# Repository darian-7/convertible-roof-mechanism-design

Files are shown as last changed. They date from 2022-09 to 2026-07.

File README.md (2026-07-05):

# Convertible roof mechanism design (Fiat 595 Abarth)

**A full mechatronic design of a powered convertible roof for the Fiat 595 Abarth, from the MATLAB motor and damping dynamics to a Fusion 360 assembly and Arduino safety sensors.**





University of Bristol Year 2 Engineering Practice group project. The brief was to design a working powered roof for the Fiat 595 Abarth and carry it the whole way: market research and concept selection in Linkage, the mechanism dynamics in MATLAB, CAD and FEA in Fusion 360, material selection in Edupack, and a set of Arduino safety sensors, finishing with a bill of materials and a design review.

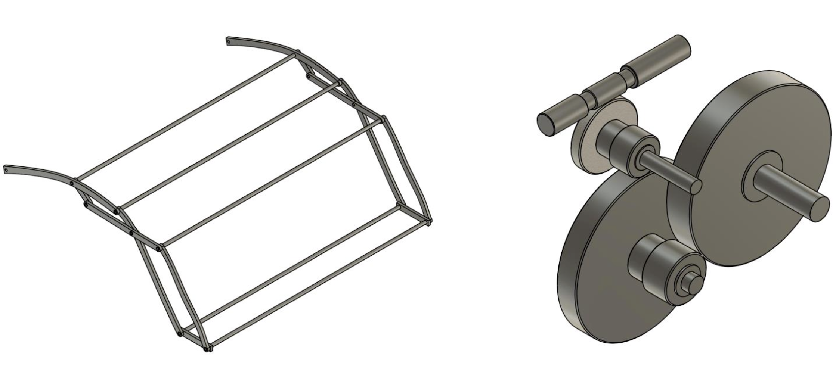
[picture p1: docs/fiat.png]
Fiat 595 Abarth


## What's inside

### Roof dynamics (`basic_model.m` and variants)
The roof is modelled as a driven rotating mechanism turned by a brushed DC motor. An ODE45 solver integrates the roof angle and angular velocity across the deploy and retract cycles from a torque balance: the motor's torque-speed line, gravity, viscous damping, aerodynamic drag read from a lookup table (`aero.m`), and a centre-of-mass radius that changes through the motion, exported from the Linkage model (`radius.m`). From that it computes torque, power, and energy for each candidate gear ratio. The deploy cycle came out at roughly 647 J. `GRAPHSFORREPORT.m` collects the design iterations (constant radius, variable radius, and the aero-plus-damping variants) into the report figures.

### Safety electronics (`docs/mechatronics_code.ino`)
Four sensors guard the mechanism so it cannot close on something or run at speed. An ultrasonic sensor watches for an obstruction above the roof, a capacitive sensor detects an object in the path, an anemometer reads wind speed, and a Hall-effect sensor counts wheel rotations to infer vehicle speed. If any of them crosses its threshold the motor stops. Two PWM channels drive the deploy and retract directions.

### CAD, kinematics, and materials
The Fusion 360 roof and gearbox assembly with FEA, the Linkage models used for concept kinematics and concept selection, and the Edupack material-selection study behind the chosen metal.

## Tech stack

MATLAB (mechanism dynamics, power and energy) · Autodesk Fusion 360 (CAD, FEA) · Linkage (2D mechanism kinematics) · Arduino (safety sensor firmware) · Granta Edupack (material selection)

## Repository structure

```
convertible-roof-mechanism-design/
├── docs/
│   ├── fiat.png                     # Fiat 595 Abarth reference
│   ├── mechatronics_code.ino        # Arduino safety-sensor firmware
│   ├── Group 1a *.pdf               # design / technical / manufacturing / mechatronics reports
│   ├── 545 Graphs/                  # deploy + retract torque, power, energy plots
│   ├── Linkage/                     # concept kinematics + concept selection
│   └── Material Selection/          # Edupack indices + weighted matrix
└── src/
    ├── basic_model*.m               # roof dynamics (motor, gravity, damping, aero)
    ├── aero.m, damping.m, radius.m  # torque contributions + variable COM radius
    ├── GRAPHSFORREPORT.m            # report figures across design iterations
    └── *.f3d                        # Fusion 360 roof + gearbox CAD
```

## Notes

Group coursework project, shared as a portfolio reference. Please don't submit any of it as your own.

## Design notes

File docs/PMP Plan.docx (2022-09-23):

# Template Project Management Plan

# 1 Introduction

The aim of this project is to produce a detailed design report for a convertible Fiat 595 Abarth that puts itself in direct competition with the BMW Mini Cooper convertible. Acting as the engineering team at Abarth, the following report presents a ‘proof-of-concept design’ for the Fiat with the goal of taking the idea forward into detailing and production based on the concept’s viability for a convertible 595 Abarth.

# 2 Project scope

Scope of project (Work Breakdown Structure):

- Market research, stakeholders, and priorities with a PDS.
- Concept selection using FBDs, Lego, and Linkage + CAD design.
- Modelling: motor and gear ratio combinations, system damping, gearbox efficiency, COM, mechanical power, power vs torque graph, radius vs angle of mechanism graph, angle vs time for retracting/deploying mechanism graph, mechanical power vs time.
- Manufacturing planning of chosen component + technical CAD drawing.
- Material selection and costing of all materials intended to use.
- Mechatronics report on chosen safety features and their respective sensors for the convertible roof mechanism.
- Motor and gear combination choices + CAD design of gearbox.
- Design evaluation of success of entire proposed report highlighting successes and failures.

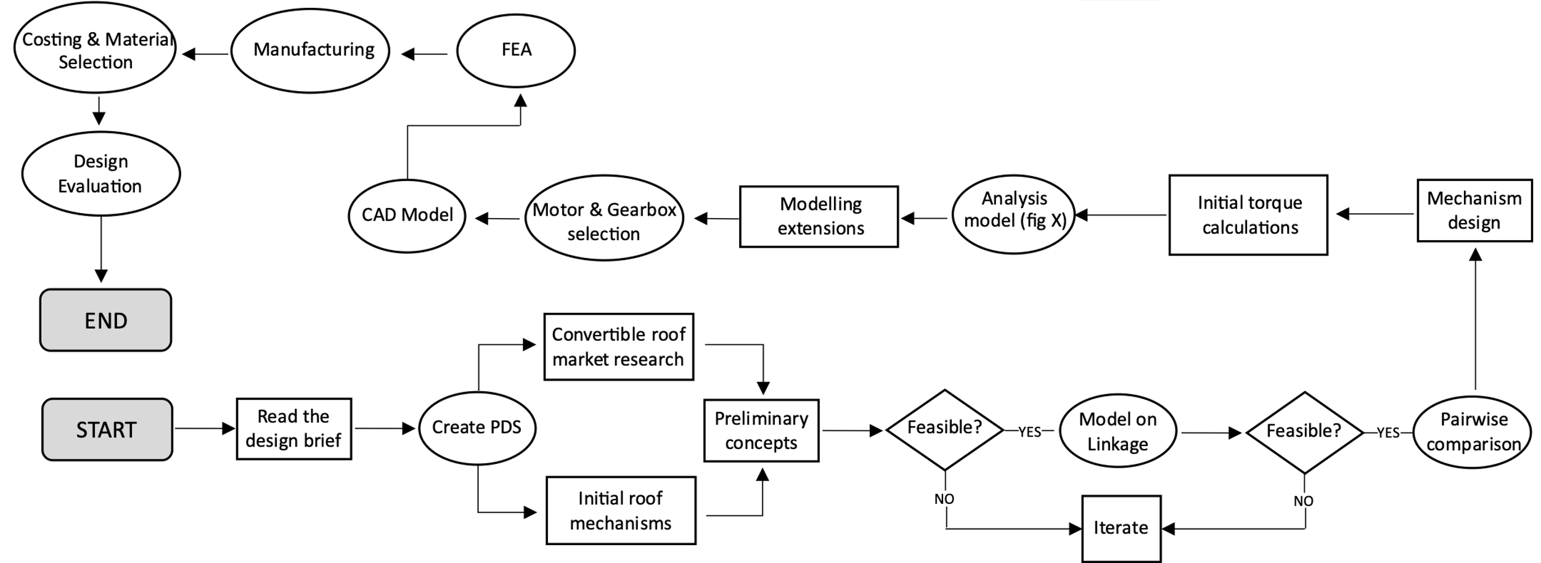
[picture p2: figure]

Not in the scope of project:

- Real-life sensor functionality with car based on its intended use.
- Real-life testing of retracting/deploying roof mechanism of Fiat 595 Abarth.
- Real-life testing of the chosen gear ratios and selected motor.
- Testing the life-cycle of the convertible Fiat 595 Abarth as it is not manufactured yet.
- Market research involving surveys to identify the needs of the required target market, not in the scope of the project due to time constraints.

## Key success criteria

- Come up with safety features that put the safety of the passengers and convertible roof mechanism as utmost priority.
- Design convertible roof report that contains similar features to the convertible Mini Cooper and remains within a similar price bracket to put it in direct competition with the convertible Mini.
- Conduct sufficient market research
- Aim to meet most, if not all of the requirements listed in the PDS of the report.
- Aim to stay in track with the recommended timelines given to us in the brief.
- Run iterations and constantly develop concepts and design decisions to produce the best possible ‘proof of design’ report. Important to do this throughout the report and not at the end of the report.

## 2.1 Project assumptions

- Assumption 1: Group 1 acts as the engineering team at Abarth and the project is a ‘proof of design’ report made with the goal of taking the convertible roof idea forward into detailing and production for the Fiat 595 Abarth to put it in direct competition with the convertible Mini Cooper.
- Assumption 2: Us as the engineering team has access all components required to manufacture the convertible roof: Roof bracket, motor, chosen gears, chosen sensors, manufacturing methods.
- Assumption 3: Us as the engineering team have the budget to manufacture the components of the roof and conduct any required R&D throughout the design of the convertible roof mechanism.

# 3 Project team & stakeholders

Role | Responsibility | Who
Market research and PDS requirements | Market research on convertible roof concepts and features of BMW Mini Cooper convertible. Constructing a PDS which provides guidance for chosen design decisions and concepts. | Darian
Manufacturing, material selection and costing | Details on manufacturing process of chosen component. Material selection process with appropriate justifications. Costing of chosen components need to manufacture the convertible roof mechanism. | Andhika, Darian
Drawings | Complete technical drawing of chosen component. Complete assembly drawing of the roof. Layout diagram showing gearbox arrangement. All drawings done on Fusion 360. | Andhika
Motor, gears, and gearbox | Selection of motor and gear ratio. Gearbox arrangement based on required system energy and torque. | Viral and Andhika
Modelling | Model of inverse pendulum, motor/gear combinations, gearbox efficiency, system energy use and COM. All calculations are coded on MATLAB and the graph outputs are explained in the report. | Viral
Iterations and design evaluation | Evaluation at the end of the report highlighting the success of the overall ‘proof of design’ report and a discussion of what could be done better. | All
Mechatronics | Selection of appropriate safety features and the sensors they use. Hardware schematic diagram of sensors. Arduino source code that uses the outputs from the sensors to signal the microcontroller. | Darian

## 3.1 Communication plan

Audience | Purpose & type of message/content | Communication channel | Frequency | Owner
Engineering Team | To track weekly progress with a Gantt chart and to ensure all members are kept up to date with concurrent work. | In person for majority group work, MS Teams for quick updates and weekly meetings. | 2x/week for group work and short online updates weekly. | Andhika, Viral, Darian
Project Supervisors (Professors) | To obtain feedback and constructive criticism throughout work to iterate work to conform to given feedback. | Submission gates & weekly in-person EngPrac lectures. | Weekly and dates given below in section 4. | Chris Snider

# 4 Project timeline

8-week project consisting of 5-day weeks – 40 days of official working time.

Stage-gate submission points:

Friday March 4th – Feedback stage gate 1

Monday March 21st – Feedback stage gate 2

Technical Drawing Friday 29th April 12pm – Design FREEZE

Final report due Thursday 5th May

# 5 Risk register

Ref. | Category | There is a risk that… | The consequence would be… | Likelihood (1-5) | Severity (1-5) | RF | Mitigation Action
1 | Project | Team member(s) are unable to carry out work because of COVID-19. | Fall behind on specific components, potentially delaying entire project. | 1 | 3 | 3 | Delegate work to others and try and work slightly ahead of schedule for extra leeway.
| Project | Not defining our priorities coherently | Design decisions made by group members can individually vary and a result in a broadly designed product | 3 | 4 | 12 | Ensure the brief is understood well and priorities clearly stated in the beginning of the report.
| Project | Project schedule is not clearly defined or understood | Potentially not meet allocated deadlines | 4 | 3 | 12 | Hold scheduling meetings weekly so that the plan is understood, and the likelihood of missed task is reduced
| Project | Project load not evenly distributed between group members | Overworking a team member and resulting in a lower quality outcome | 3 | 3 | 9 | Delegate deliverables to group members evenly at the start of the project and if it is uneven, some work can be handed over to a member with more time
| Project | Insufficient understanding of the brief | Deviation from the scope of the project | 2 | 3 | 6 | Thoroughly read the brief individually and with the project team and note down key information
| Project | Lack of communication between group members | individual tasks can deviate and possibly take forward an incorrect design decision | 3 | 4 | 12 | Weekly meetings to collate information on the tasks that have been completed within the last week
| Project | Arbitrarily reducing task durations and run tasks in parallel | Not completing tasks to a high enough standard | 4 | 2 | 8 | Ensuring a method for project management is enforced and the time spent for tasks are sufficient
| Project | Scope creep | spending more time on things that you don’t plan on considering | 3 | 2 | 6 | Document the project scope in the initial group meeting and ensure its authorised by the project manager
| Project | Unplanned work that must be accommodated | Can have effects on other member’s work and time needs to be spent reconsidering the unplanned work | 4 | 3 | 12 | Discuss new work during weekly meetings and discuss a plan of action to try and minimise the setback
| Project | Loss of documentation / failure of software | Hours of work lost and would need to be recompleted | 1 | 5 | 5 | Ensure that all documentation and work is frequently saved and if an auto-save feature is present, ensure its used.
| Technical | Failure of mechanism due to excessive wind/car speeds | Danger to passengers and other road users | 1 | 5 | 5 | Sensors – airflow and hall effect sensor
| Technical | Personal injury due to moving parts | Loss of fingers and legal action can be taken by customers | 1 | 5 | 5 | Sensors – capacitive proximity and casings
| Technical | Lack of resources or supply chain issues | Delay in production and therefore not meeting the lead-times | 3 | 4 | 12 | Constant communication with suppliers so that any setback can be resolved immediately
| Technical | Loose components | Unwanted oscillations, noise, and possible failure of system | 2 | 5 | 10 | dampers and fixings
| Technical | Gear could jam due to debris. | Roof failing mid-deploy could pose great consequences I.e. in extreme weathers | 1 | 4 | 4 | Ensure mechanism is covered and not fully exposed: no entrance points for debris into gearbox.
| Technical | Calculation/model errors | Roof failing and putting passenger at risk of danger | 2 | 5 | 10 | Stringent modelling testing to ensure that the model functions as it should

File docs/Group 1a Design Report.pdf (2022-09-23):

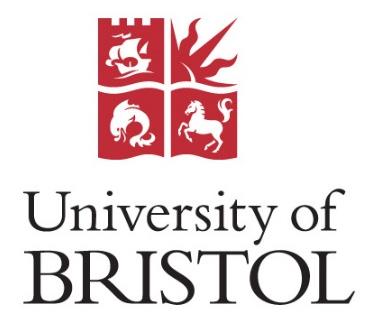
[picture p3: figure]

## Fiat 595 Abarth Convertible Roof Mechanism Design

Group Members: Darian Irani (en20703), Viral Shah (di20467), Andhika Nasution (ei20239)

Group 1a

Report date: 06/05/2022

Abstract

The assignment was to design a convertible roof mechanism for the Fiat 595 Abarth with an aim to put it in direct competition with the BMW Mini Cooper convertible. This report aimed to test the feasibility of a proof of concept, with the goal of mass production. Through the several stages of the project, concepts were rigorously assessed prioritising cost and safety and maintaining level performance. Combining technical analysis with thorough mechanical design, it was decided that this system would be developed and taken forward to the engineering team at Abarth.

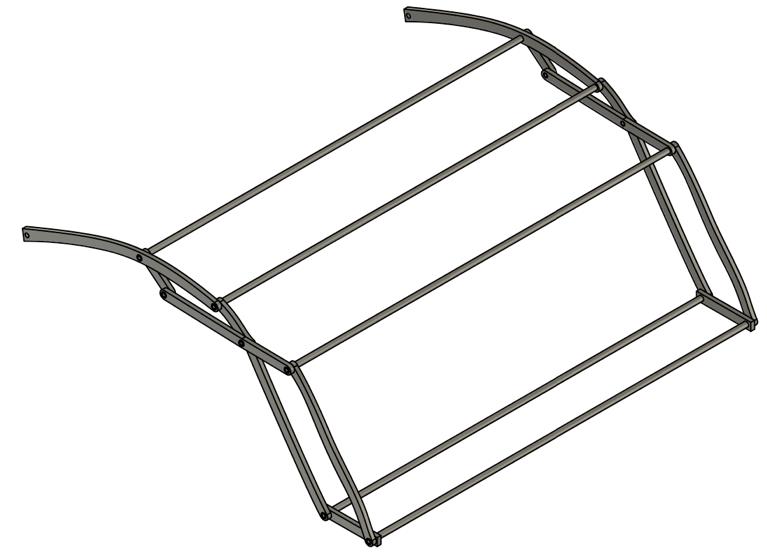
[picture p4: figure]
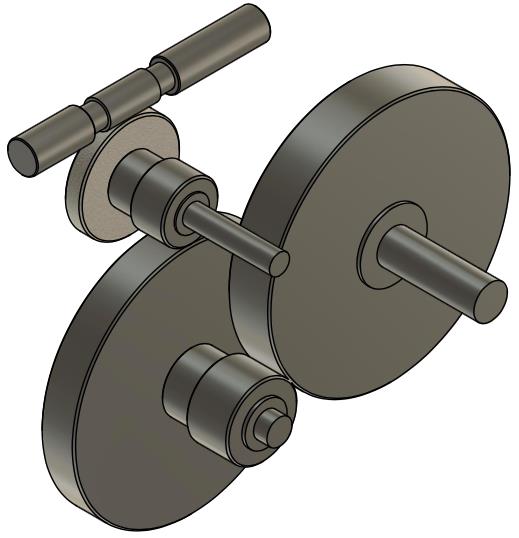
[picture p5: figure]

### D1. Introduction

This project aims to produce a detailed design report for a convertible Fiat 595 Abarth that puts itself in direct competition with the BMW Mini Cooper convertible. Acting as the engineering team at Abarth, the following report presents a ‘proof-of-concept design’ for Fiat to take the idea forward into detailing and production based on the concept’s viability for a convertible 595 Abarth. As a result, the report possesses a detailed consideration of the technical
requirements, concept designs, motor & gearing
analysis, gearbox layout, and design iterations.

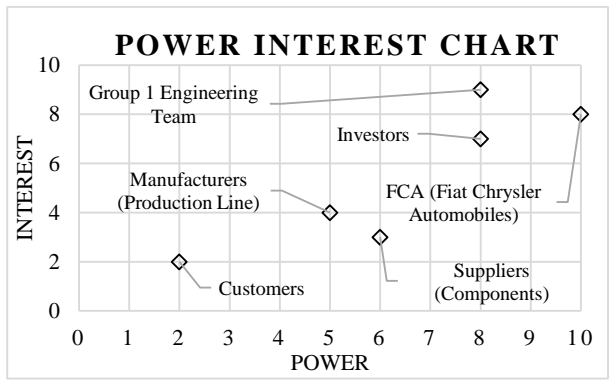
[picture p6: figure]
Group 1 Engineering; Team; Investors; (Production Line); Manufacturers; FCA (Fiat Chrysler; Automobiles); Customers; Suppliers (Components); INTEREST; POWER; POWER INTEREST CHART

Fig. 1 gives a numerical representation of stakeholder groups who have a direct interest and influence over the project – including manufacturing, performance, and overall quality control. Fig. A in the appendix provides a more detailed matrix about each stakeholder group.

Key priorities in the design were cost and safety. Cost was deemed a necessity due to the nature of this car within the market of affordable hatchbacks. Additionally, safety was prioritised with regards to customer satisfaction as well as investors reputation and likelihood to encourage further support. Two key assumptions made were: the engineering team has access to all components required to manufacture the mechanism – roof bracket, motor, gears, sensors & manufacturing methods; the engineering team has available budget in order to manufacture and conduct required research & development throughout the design process.

Fig. 2 displays an outline of the design process in the following report, showing a visual representation of how design decisions were made and how one output led to another. It shows the points in the report where the feasibility of concepts is questioned, indicating where iterations of the design were to be made.

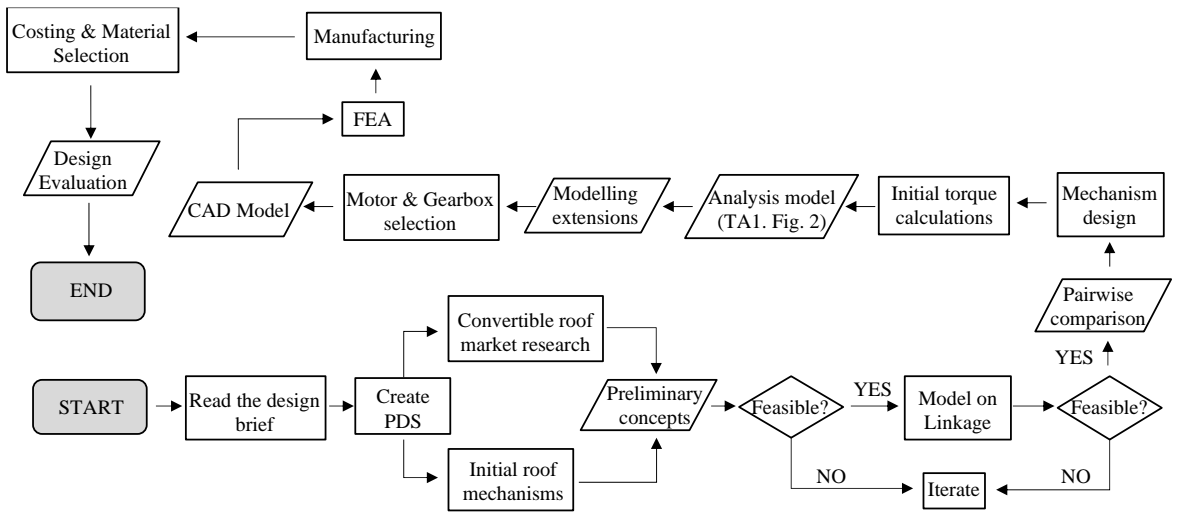
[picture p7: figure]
START; Read the design; brief; Create PDS; Convertible roof market research; Initial roof mechanisms; Preliminary concepts; Feasible?; Iterate; YES; Model on; Linkage; Pairwise comparison; Mechanism design; FEA; Initial torque calculations; Analysis model (TA1. Fig. 2); Motor & Gearbox selection; Manufacturing; Design Evaluation; END; CAD Model; Costing & Material Selection; Modelling extensions

### D2. PDS

The PDS was generated using the design brief, market research and engineering intuition. The quantities in the target and limit columns were referenced from convertibles on the market and the MINI Cooper convertible. All the requirements are testable prior to the manufacturing of the car to supplement the design of the convertible Fiat. The requirements have a 5 to 1 priority ranking depending on their importance to the overall design of the roof where 5 is the utmost priority and 1 is the least priority. The highlighted requirements (1,
18) portray those not assessed in the PSS.

Figure 1: Power-Interest chart for stakeholders

Figure 2: Flowchart depicting entirety of design process with ref. to Analysis Flowchart (TA1. Fig. 2)

### D3. Concept generation

5 concepts were first sketched on paper as an initial prerequisite. Lego was then used as a basic reference, which was then translated into 3 concepts simulated in Linkage software as seen in Figs. 3, 4 and 5. This was an iterative process of using folding techniques along with Gruebler’s Equation [18] (ensuring the number of members and joints coincided with degrees of freedom) and changing the geometry of members until they were fully extended and folded within the required dimensions. To gain a more accurate perspective of scale, an image portraying car dimension was overlayed onto the concepts (as seen in Figs. 3 to 6). Additionally, the test for cycle duration at this stage was simply a relative comparison between all the systems, with input rpm being an arbitrary constant common among the concepts.

Table 1: Product Design Specification (PDS)

No. | Category | Requirement | Target | Limit | Test Method | Rank (5-1)
1 | Safety | Should not interfere with headspace of passengers | 150mm above headrest [1] | 100mm above headrest | Run simulation on Linkage software | 5
2 | Safety

Roof should be able to withstand a certain weight

3000N [2] | 2000N

Fusion stress analysis
on mechanism.

5

3 Safety

Terminate folding process if obstacle is interfering with folding process

Obstacle detected 8mm
away from car

Obstacle detected when
in contact with car

Test sensor with
Arduino

5

4 Safety

Terminate folding process if car is above certain speed

Process is terminated if
speed > 20mph

Driver is alerted if speed > 20mph

Test sensor with
Arduino

5

5 Safety

Terminate folding process if insufficient space above car

300mm above car | 500mm above car

Test sensor with
Arduino

5

6 Safety

Terminate folding process if headwind speed is too high

Process is terminated if
speed > 20mph

Driver is alerted if speed > 20mph

Test sensor with
Arduino

5

7 Performance

Components of roof should not be too complex

Total no. of members
and joints: 25

Total no. of members
and joints: 35

Run simulation on
Linkage software

4

8 Performance

Folding mechanism should not use too much torque

Distance between
deployed roof COM and
pivot point: 600mm

Distance between
deployed roof COM and
pivot point: 800mm

Run simulation on
Linkage software

3

9 | Performance | Roof must operate perfectly in adverse weather conditions

Weatherproof casing for
gearbox and joints

Weatherproof casing for
joints

Market research for
weatherproof casing

4

10 | Performance | Folding process should be linear

Cycle time evenly split
between motion phases

As balanced as possible

MATLAB inverse
pendulum model

2

11 | Performance | The roof must open and close within a given time
15 seconds [1] | 20 seconds

Simulate model on
MATLAB

5

12 | Size | Roof must attach in given area

Attach in 80x80mm
area [3]

Attach in 80x80mm area

Run simulation on
Linkage software

3

13 | Size | Roof must fold in given area

Fold in 670x280mm
area, width 1204mm [3]

Fold within 670mm
length, width 1204mm

Run simulation on
Linkage software

3

14 | Size

Total mass of roof mechanism should not exceed specified amount

25kg [4] | 30kg | Fusion model | 4
15 | Size | Roof should be within a specified swept height
300mm above car [1] | 500mm above car

Run simulation on
Linkage software

3

16 | Material | Mechanism should be recyclable | 60% recyclable material

At least 30% recyclable
material
Material selection | 2
17 | Material | Mechanism should be corrosion resistant | Non-oxidising material [5]
Corrosion resistant paint

Specs from Edupack
software

3

18 Maintenance

Every component of roof must be detachable for servicing

Metal bracket and
canvas replaceable
(100% replaceable)

Canvas must be
replaceable (50%
replaceable)

Design decisions of
the convertible roof

3

19 | Maintenance | Components should be available by industrial standard | 100% of components sourced via catalogues | 50% sourced via catalogues | Market research on catalogues | 3
20 | Cost | Overall cost of roof mechanism | £500 [1] | £1000 | Bill of materials | 5
21 | Aesthetics | Geometry should follow 595 Abarth roof structure | Follow curves of base model 595 | Ensure no sharp turns in geometry | CAD model | 2

D3.1. Concept 1

Looking at concept one (see Fig. 3), the applied mechanism was a derivative of the scissor mechanism. This is a low complexity, 5-bar design. Prioritising cost and performance, the simplicity of this design could reduce manufacturing costs and
potentially increase reliability as fewer components
are interacting with each other. This mechanism also

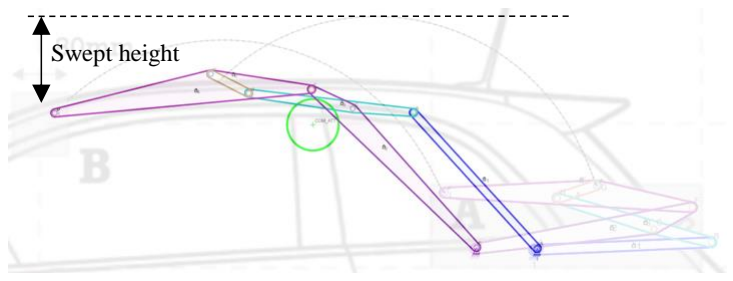
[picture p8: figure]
Swept height

does not interfere with the headspace of the passengers (PDS Requirement 1) which was tested on Linkage. Simulating opening the mechanism, the motion leaves an approximate space of 150mm between the roof and the user. The way concept 1 is designed, the swept height was minimised with a measured value of 253mm (Requirement 15). Reducing this reduces the overall surface area in contact with the air when opening, which can allow for the roof to be opened at greater velocities as the overall drag is reduced, in turn promoting safety.

D3.2. Concept 2

Concept two uses a 7-bar system, utilising a scissor
mechanism with a front section that retracts backwards as it opens. This happens through the triangle of linkages connecting members 4, 5 and 7 as seen in Fig. 4, providing a creative way to collapse the roof. However, looking at the aforementioned triangle, there would be a high value of torque running through link 6, as the centre of mass is too far away from the pivot. Due to the way link 7 retracts,
the swept height is much greater than the other
concepts with a value of approximately 700mm.

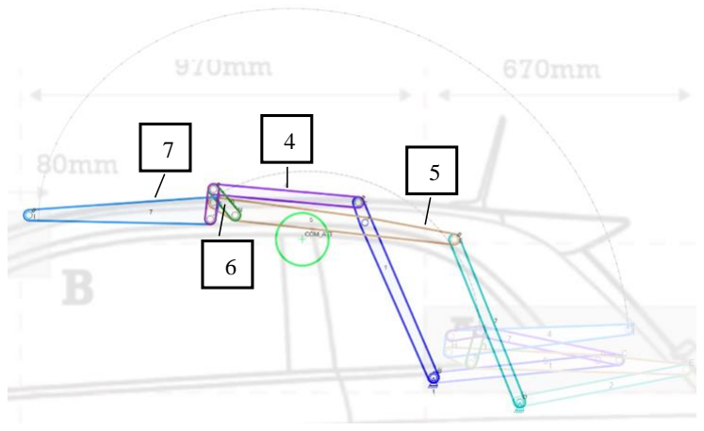
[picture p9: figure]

Having a large swept height would result in greater drag when opening the roof whilst the car is moving, therefore, stringent stress analysis testing must be implemented to ensure the safety of the passengers.

D3.3. Concept 3

Finally, concept three is another form of a scissor
mechanism, however, this time being a 10-bar system. This utilizes the most linkages out of all
concepts, | which | could | lead | to | a | higher
manufacturing cost and added complexities in maintenance. The fact that this is a common design
throughout all linkage systems proves that it is a
somewhat reliable concept, however, in this

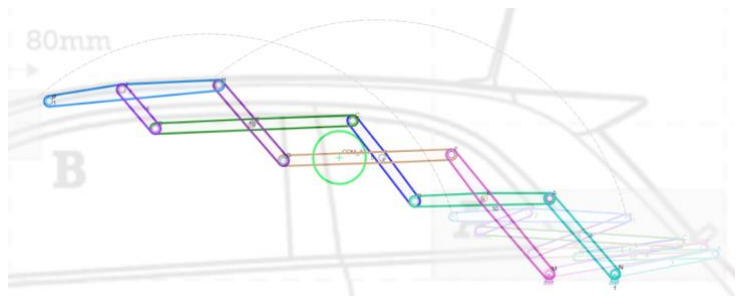
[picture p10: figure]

implementation having many links causes the length scaling and geometry to interfere with the back seats when fully extended. This poses a potential safety hazard. The swept height for this concept is the best of the three at 140mm, again allowing the operation of the roof to be more streamlined under higher wind speeds.

D3.4. Concept Selection Criteria

To determine the most suitable concept to take forward, a Pairwise comparison matrix found in Table 3 was used to compare the three concepts against weighted selection criteria. The calculated weightings shown in Appendix Table A uses important requirements from the PDS in Table 1. Each criterion, shown in Table 2, use different metrics to measure how they differ from each of the 3 concepts.

D3.5. Selected Concept

Table 3 displays a numerical representation of how each concept scored against the 7 criteria and their respective metrics. A ranking of ‘5’ being the best and ‘1’ being the worst, as a result, concept 1 scored the

Figure 3: Concept 1

Figure 4: Concept 2

Figure 5: Concept 3 highest overall percentage. This is reflected by concept 1 for its minimal components and joints, resulting in a low mass system with realistic costs and torque requirements.

Although it ranks second for its maximum swept height, it is only 80mm higher than concept 3 which ranked first. Finally, concept 1 also ranked first for its safety as it interferes the least with the backseat passengers’ headspace, which ultimately results in the best stowed away size. Therefore, the consensus was to go ahead with concept 1 as the selected concept since it scored the highest in the weighted matrix and is most in line with the requirements stated in the PDS.

### D4. Mechanism Design

Note: Motor, gear ratio and damping coefficient selection was carried out using the retraction model, as this is what had the longer cycle time when compared to deployment. The holding ratio was the gear ratio needed to keep the mechanism in a deployed (unattached) position, as retracting from here needs the highest torque.

D4.1. Geometry Iteration

As an iteration for the design of the members, the geometry was altered so that the roof mechanism would be more realistic. The previous design consisted of straight members as seen in Fig. 6, but the problem arises when the roof material lays over the system. The top of the Abarth 595 has a smooth gradient throughout so replacing it with clear-cut straight edges will negatively affect the aesthetics of the vehicle. The roof geometry was revised so that the outer members in contact with the roof provided a smooth gradient seen in Fig. 7, thus, further satisfying Requirement 21 in the PDS.

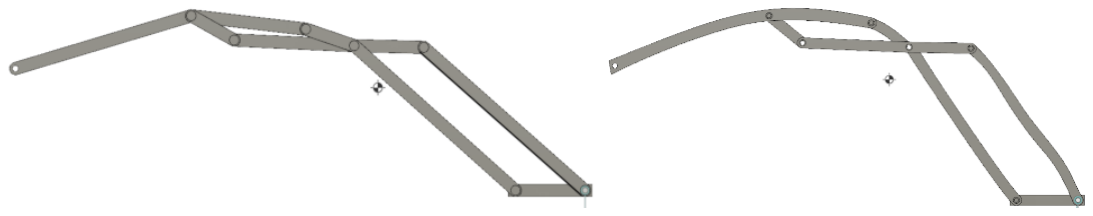
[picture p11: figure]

D4.2. Material Selection

Where ρ is density, E is Young’s modulus, Cm is the cost per unit mass and σy is the yield stress.
The material selected for the roof mechanism was found by applying conflicting objective equations and determining a corresponding material index. Minimising mass and cost were the primary objectives which further align with Requirements 14 and 20, respectively, in the PDS. A stiffness and strength constraint were applied, modelled for a beam of length L and force F to represent a single member in the system. In both stiffness and strength limited design, the free variable was the material (density) and the area of the beam.

Table 3: Pairwise comparison matrix

Table 2: Concept selection criteria metrics

Figure 6: Initial member geometry | Figure 7: Concept 1
Complexity - proportional to the number of joints the concept requires. | Safety - measured by considering how much space the roof takes up inside the car during its folding process.
Max Height - the tallest point of the roof during the folding process. | Cost - proportional to the sum of members and joints the concept requires (assuming each member costs the same).

Mass - proportional to the number of
members the concept requires.
Torque - distance between the concepts’ COM and its pivot point.

Stowed Away Size - the dimensions of the roof when folded.

MStiff ,Mass = ρ | E | (1) | Mstiff ,Cost = Cm ρ | E | (2)

MStrengt ℎ,Mass = ρ (σy

)

2
3 | (3) | MStrengt ℎ,Cost = Cm ρ (σy
)

2
3 | (4)
| Criteria | Complexity | Max height | Mass | Torque | Safety | Cost | Stowed away size
| Weights | 0.130 | 0.193 | 0.028 | 0.021 | 0.363 | 0.245 | 0.021
Options | | 1 | 2 | 3 | 4 | 5 | 6 | 7 | Total | %
Concept 1 | 1 | 4 | 2 | 3 | 2 | 4 | 4 | 3 | 3.524 52.3
Concept 2 | 2 | 2 | 3 | 2 | 1 | 2 | 2 | 2 | 2.172 | 32.2
Concept 3 | 3 | 1 | 1 | 1 | 3 | 1 | 1 | 1 | 1.042 | 15.5

The loading conditions modelled for both design scenarios were a simply supported universally distributed load which was concluded to be the most accurate depiction for a convertible car roof. After eliminating the free variable, the material indices for stiffness and strength limited design can be seen in (1), (2), (3) & (4).

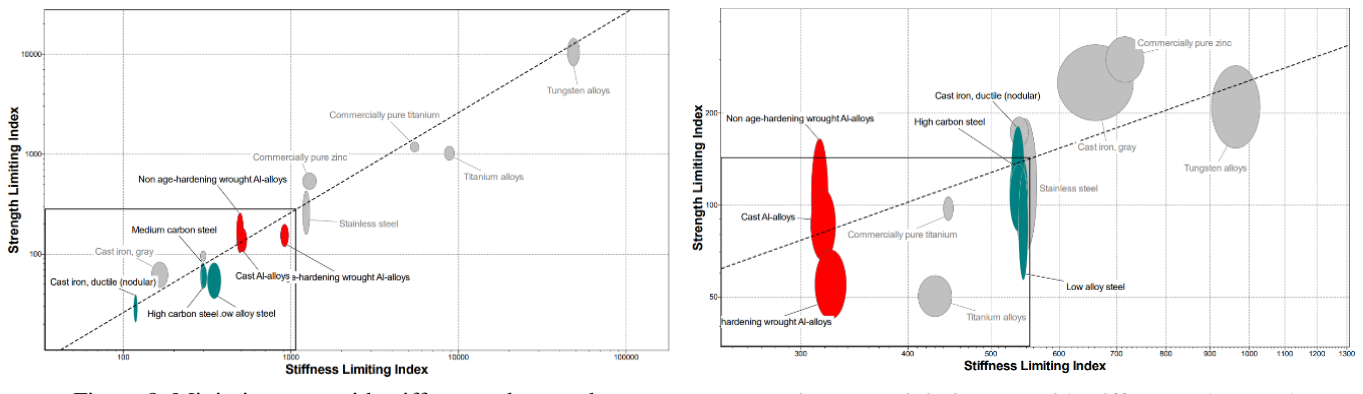
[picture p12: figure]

On Granta Edupack [7], 2 graphs were plotted of the material indices MStiff,Mass against MStrengtℎ,Mass, and Mstiff,Cost against MStrengtℎ,Cost seen in Figs. 8 and 9. A line representing the indices’ coupling constant, was plotted on each graph alongside a box selection with the limits of required strength and stiffness. Edupack conveniently narrows down the material options so that only materials within both box selections remain.

For a robust method to compare the remaining materials, a weighted matrix with criteria: density, cost per unit mass, Young’s modulus, yield strength, tensile strength and compressive strength was used, shown in Table B in the appendix. Each criterion was assigned a weighted value, dependent on its importance, with values for each criterion completely sourced through the material data sheets on Granta Edupack. Each material was then given a score depending on how well it performed in each criterion with the final material determined to be low alloy steel.

D4.3. FEA Stress Analysis

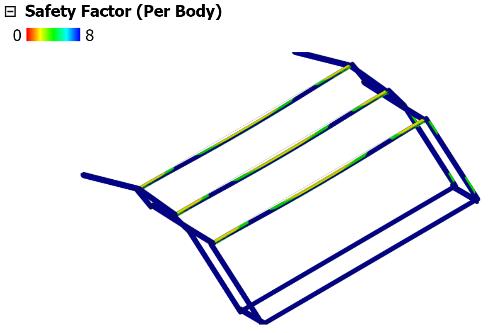
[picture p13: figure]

As a final consideration for the definitive design, an initial CAD model was developed in Fusion 360 with an assumed bar thickness of 12mm. Applying a static stress simulation when the system is deployed, the outputs can be analysed such that a compelling value for thickness can be determined. Minimizing thickness decreases the overall mass of the system and in doing so, follows Requirement 14 in the PDS. The simulation was also tested against Requirement 2.

For the initial loading case, a static stress simulation was conducted. The effects of gravity, universally distributed loads and wind loading were applied normally across each face of the top beams
with a magnitude of 2000N. The study material chosen was low alloy
steel which was determined in the D4.2.

When analysing the simulation results, the safety factor, Von-Mises stress and displacement were the outputs taken into consideration. From the safety factor output graphs, it is clear that areas with the lowest safety factors are situated on the lateral beams which are connecting the two mechanisms. The lowest minimum safety factor was 1.041 as seen in Fig. 10, which is not within a particularly safe region, but sufficient for the limits of Requirement 2. Nevertheless, the safety factor across the other beams can be seen in blue, meaning that the value can lie from 6 to 15 which is within a comfortable safety range. An argument can be made that it is unlikely a load of 2000N would be experienced, however as a safety concern, when the car is travelling at a high velocity alongside harsh weather conditions, the roof can be exposed to excessively high loads. A solution to improve the safety factor in the lateral beams was to increase their diameter, whilst maintaining the same thickness for the remaining beams. Extending this, the results from the Von Mises stress and displacement analysis support the lack of strength in the lateral beams as the greatest deflection and stress

Figure 8: Minimise mass with stiffness and strength limited constraint

Figure 9: Minimise cost with stiffness and strength limited constraint

Figure 10: Safety factor stress analysis results when deployed.

concentrations occur in the middle of the members. Changing the diameter of the lateral beams to 15mm and repeating the static stress simulation when the roof is closed gives a minimum safety factor of 1.516 which now satisfies Requirement 2 in the PDS as the minimum load the roof can now withstand is 3032N.

D4.4. Fixings & Joints

The material selection process in D4.2 influenced the decision of choosing Alloy Steel plate 4140 material for the metal bracket of the convertible roof. Table 10 contains a full bill of materials showing all parts needed for the required fixings. The first type of fixing is a bush fixing at each of the 14 joints, which attach the ends of each member. The bush prevents friction between the joints and allows the joints to slide without wear in a rotary-like movement. This fixing uses a clearance fit at each joint where the bar is slightly slimmer than the rod holes. Additionally, a 1mm chamfer is machined into each member to aid assembly. This type of fit uses an h6H7 tolerance that is chosen to allow a hinge-like movement, which is important for the opening and closing of the convertible roof. Lateral movement in the joints and their members could lead to unwanted torsional stresses caused by wind forces or centrifugal acceleration. Therefore, two bearings are placed on each horizontal member to account for lateral displacement, using interference fits with p6H7 tolerances. The chosen bearing has a bore diameter of 15mm and the p6H7 tolerance leads to a 15.015-15.024mm range. The tolerancing and upper/lower bounds for diameter use Tables C and D in the appendix. The mechanism should work perfectly in adverse weather conditions as per PDS requirement 9; therefore, a waterproof covering is used to prevent rain from rusting the joints and dust from entering the joints’ cavity.

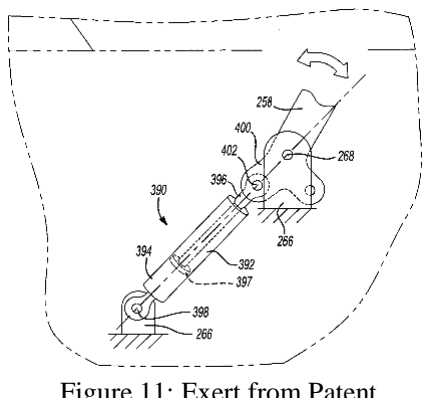
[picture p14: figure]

### D5. Damper Design

As outlined in TA2.3. damping was a feature, physically considered in the
design to keep the utmost accuracy.

D5.1. Linear Damper

Firstly, a linear damper was added to the mechanism. Fig. 11 [8] show a design that inspired the final design used in this project, which is highlighted in Fig. 12. The Associated Spring Raymond [9] catalogue was used, and it was identified that using this type of configuration limited the cylinder length to 300mm. From this filtered selection, the 275.08mm damper was chosen as this offered the highest damping coefficient. Between the mechanism pivot and damper pivot, a connecting rod was used with radius equivalent to the stroke length, 101.6mm. The first and third lines show the points at which the damper is fully extended, with the second line showing the point of greatest compression. The dimensions on Fig. 12 differ to those stated previously as a different scale was used. The arc represents the path followed by the connecting joint, equivalent to part ‘402’ from Fig. 11 and ‘pivot a’ represents ‘part 266’ on this same figure, which allows the damper to rotate and compress/extend through this motion.

D5.2. Rotational Damper

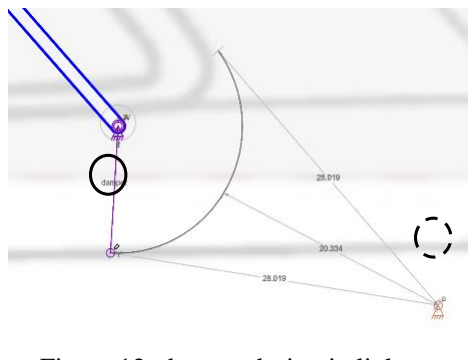
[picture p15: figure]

Secondly, a rotational damper was considered, being fixed onto the initial layshaft in series with the motor. This would avoid using any connecting rods and directly apply torque to the input of the mechanism. In comparison this was a much simpler design, with the gearbox being joined in between via a pinion.

D5.3. Final Design

Whilst TA2.3. explains how the results from the linear damper were inferior to those from the rotational damper, the design also played a part in choosing against it. The main reasons were the scale and how much space the configuration took up. Also, being a dynamic system with moving parts, there extra joints and fixings which decrease the overall safety of this feature and is more prone to required maintenance and hence lifetime cost, which were two priorities of this project. On the other hand, rotational dampers have no moving parts

Figure 12: damper design in linkage

Figure 11: Exert from Patent US7275783B2 showing how the damper connects and extends as the mechanism moves.

and are permanently sealed, making them more durable and requiring little maintenance [10]. The high viscosity fluid inside the damper also absorbs external shock and vibration, therefore increasing its safety.

### D6. Motor, Gear Ratio & Damping Coefficient Selection

D6.1. Initial Motor Analysis

Through the design brief, it was required that DC motors from the Bosch catalogue, [11] without transmission were to be used, powered by the car battery at 12V. The motors chosen to carry out analysis were the APM and NSA-I motors. These were chosen because they featured clockwise and anti-clockwise rotation – a trait that prevents the need to implement a reverse gear train in the gearbox, in turn saving on mass and cost. The initial model also assumed a system mass of 20kg, which was then accurately calculated in D4.2. found to be 23.5kg and included in 6.2. Table 4 shows holding ratios for all motors.

Initially, with only the motor and gravity acting on the system, the four motors were tested with gear ratios 1% above their holding ratio. Depicted in Figs. 13 and 14 and are their retraction times and efficiency, showing that the APM motor was the closest to the required cycle time, as well as having the highest efficiency. On the other hand, it was noted that the gear ratio was also the highest at well over double all the NSA-I motors. As extensions were added to the model to increase resistive torques to the mechanism, the gear ratio was predicted to increase due to this motor’s very low stall torque. This was an important factor when considering gearbox design as higher gear ratios lead to larger, heavier, and more expensive gearboxes, and with cost being a design priority this resulted in the APM motor being discarded. The NSA-I 2 motor was also set aside, but not discarded, due to its very high running speeds and high nominal power as per the Bosch Catalogue. This left NSA-I 1 and 3, the latter having the second highest efficiency. Therefore, the NSA-3 motor was chosen at this stage, even though it had a very quick cycle time.

D6.2. Final Motor Analysis

In this section the complete model, inclusive of 20mph oncoming wind, was considered. The gear ratio and damping coefficient were selected as a combination and as such, iterated together. The design priorities, as per Requirements 11 and 10 in the PDS, were to obtain cycle time between 15 and 20 seconds, whilst aspiring to have motion as linear as possible. To achieve this, it was found through comparison of high and low, that higher damping coefficients favoured this motion. This is because higher speeds are affected more by damping, with lower speeds remaining similarly low across different coefficients. Due to this, a higher stall torque would be favoured as lower gear ratios would achieve similar performance to motors with lower stall torque and higher gear ratios. At first, a damping coefficient of 1000Nmsrad⁻¹ was used to compare properties of the three motors at a gear ratio of 50% above the holding ratio. The

Motor | Holding Ratio | Motor | Holding Ratio | Motor | Holding Ratio | Motor | Holding Ratio
APM | 601.4 | NSA-I 1 | 265.7 | NSA-I 2 | 238 | NSA-I 3 | 165.6

Table 4: Holding ratios for all candidate motors.

Figure 13: Cycle time for all motors

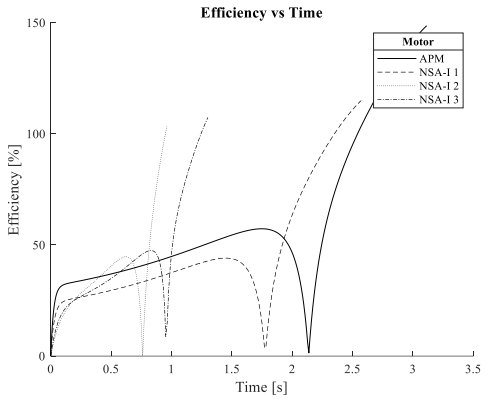
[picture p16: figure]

Figure 14: Efficiency for all motors

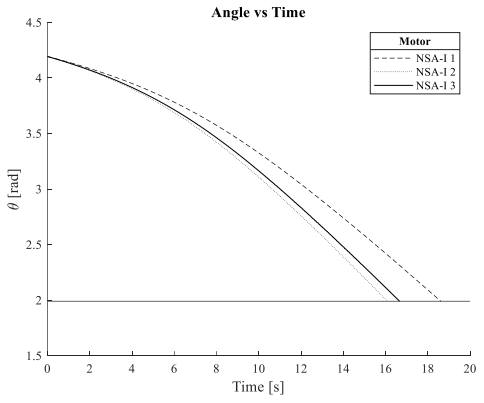
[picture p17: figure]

Figure 15: Cycle time for all motors resulting cycle times are presented in Fig. 15 for all motors. Power usage and efficiency were not priorities in motor selection; hence their outputs were not utilised – they can be seen in Figs. D and E in the Appendix.

D6.3. Final Value Selection

A manual process of checking combinations of gear
ratio, damping coefficient for different motors took place. The aim of this was to fulfil Requirement 10, hence many iterations were considered. An exert of the full process being is displayed in Table 5, showing initial combinations that did not achieve linearity and final combinations that did. The rows highlighted are presented on Fig. 16 clearly showing that a low gear ratio and damping coefficient achieve a motion with a very steep gradient. The remaining curves are all linear motions for each respective motor, and it can be observed that, from left to right, the lines become slightly more linear. When referring to Fig. 16, it is
evident that a higher damping coefficient favours a

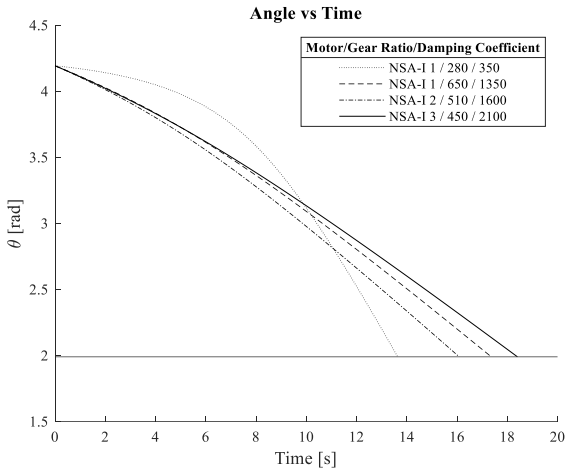
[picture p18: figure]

more linear motion – however this means higher gear ratios
are required. Adhering to design priorities, the lowest gear ratio was preferential. The NSA-I 3 motor accommodated this preference as it was the most powerful motor, and as it was the lowest gear ratio to highest damping coefficient combination (see Table 5), these were the variables chosen. Also as seen in the final column, the range of 420-450 offered linear motions whilst still being under 20 seconds, hence this was the gear ratio range used in the gearbox design. The final characteristics are presented in Table 6 and Fig. 17 below, which were found using a gear ratio of 421.45 – this exact gear ratio and how it was calculated is outlined in D8.2.

Figure 16: Cycle time for all motors

Table 5: Exert from thorough selection process, showing linear and non-linear combinations

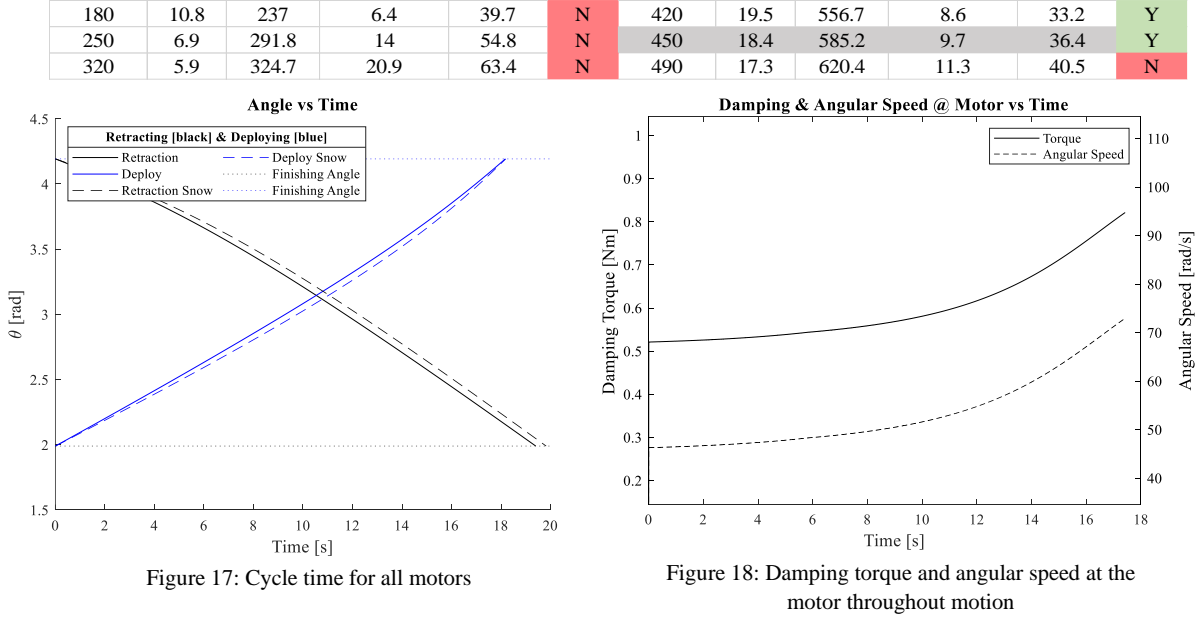
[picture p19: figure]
motor throughout motion

Figure 17: Cycle time for all motors | Figure 18: Damping torque and angular speed at the
Gear Ratio | Time [s] | Energy [J] | Efficiency [%] | Power [W] | Linear? | Gear Ratio | Time [s] | Energy [J] | Efficiency [%] | Power [W] | Linear?
| | | | | | NSA-I 1 / c = 1350Nms/rad
280 | 13.6 | 202.4 | 10.3 | 26.9 | N | 580 | 18.9 | 381.7 | 14.9 | 24 | N
350 | 9.7 | 222.7 | 18.3 | 29.8 | N | 610 | 18.1 | 396.6 | 16.7 | 25.5 | Y
420 | 8.7 | 233.1 | 24.5 | 30.3 | N | 650 | 17.3 | 409.5 | 18.6 | 26.8 | Y
260 | 10.2 | 249.3 | 5.2 | 44.9 | N | 510 | 16.1 | 518.7 | 6.9 | 38.6 | Y
330 | 6.9 | 298.9 | 9.6 | 60.7 | N | 550 | 15.3 | 541.7 | 7.7 | 41.8 | Y
400 | 5.7 | 338.9 | 14 | 74.6 | N | 590 | 14.4 | 571.2 | 8.7 | 46.1 | N

NSA-I 1 / c = 350Nms/rad

NSA-I 2 / c = 350Nms/rad

NSA-I 3 / c = 350Nms/rad

NSA-I 2 / c = 1600Nms/rad

NSA-I 3 / c = 2100Nms/rad

### D7. Damper Selection

The Kinetrol [12] catalogue was used to select the rotational damper based on the damping coefficient selected. Given that the layshaft would be turning up to a maximum rate of 697rpm, it was clear that continuous rotational dashpots (CRDs) had to be selected over vane dashpots, which were limited to turning between specified angles. This would be viable if attached to the output of the gearbox, however the torque at this stage would be far too high and in turn, result in a large 235mm x 235mm damper, weighing 12kg. This was unfeasible as in comparison, CRDs weighed in the hundreds of grams. The damper selected was model Q-CR (214g) as this had a maximum safe torque of 1.5Nm, sufficient for the maximum damping torque output of the final model. Using Fig. C in the Appendix, a viscosity of 12,500cSt was selected. As the damper was at the motor, the true damping coefficient is 2100 divided by the gear ratio, giving a final value of 4.98Nm/rad/s which is well within the effective range of 20Nm/rad/s stated on the catalogue. Final selection: Q-CRD-12500.

### D8. Gearbox Design

D8.1. Gear & Module Selection

The gears chosen to be implemented in the gearbox were a combination of spur gears and a worm and wheel. Spur gears provide the advantages of high-power transmission alongside high efficiencies ranging between 96% to 99%. When considering Requirement 20 in the PDS to minimise cost, spur gears are especially suited due to the straight cut, involute profile making it simple to manufacture, hence cheaper than alternative gears. A worm and wheel were also considered as it allows for a very high velocity ratio, whilst also staying compact in size. Further advantages include a high loading capacity, operating without noise and minimal maintenance. Consequently, the primary disadvantage of worm drives would be their low efficiency which can reach values of 40% per stage since the surfaces are subject to high friction and axial stresses. Nevertheless, when paired with spur gears, which are the most efficient gear type available, the compromise of efficiency can be justified as the size of the gearbox would be greatly reduced for the velocity ratio achieved.

The velocity ratio to be achieved in the gearbox was determined in D6.3 and found to be between 420-450. A gear module needed to be selected, where the greater the value, the more load the gear can experience. From the gear module selection graph in Appendix Fig. B, the determined value for the module was roughly estimated to be between 0 and 1. Then, the maximum power values from Table 7 were used to find a corresponding angular velocity using (5).

Where P is the power output, ω is the angular velocity, TStall is the stall torque and ωno load is the no-load speed.

it was found that increasing the module consequently decreased the balanced bending stress as the critical tooth thickness increases by M number of times [13]. Therefore, maximising the module was ideal, which minimises the experienced wear over time. Thus, a module of 1 was taken forward for use in calculations.

D8.2. Gear Stages

A multi-stage gearbox system was chosen to be implemented as it allows for a high velocity ratio to be achieved whilst not compromising the size of the gearbox. Minimising the size can also result in a reduction in mass and possibly manufacturing costs. Consequently, selecting a multi-stage system can result in greater overall efficiency losses as more friction is generated within each stage. For a spur gear, the typical value for the maximum velocity ratio is 5. Any larger than this and the size of the driven gear would not be optimised to satisfy a compact gearbox. Alternatively, the velocity ratio of a worm and wheel can reach values up to 120 but can also lead to greater efficiency losses.

P = − (

TStall

ωno load

) ω
2 + Tstallω | (5)

Table 6: Final characteristics of mechanism for selected motor, gear ratio and damping coefficient

Gear Ratio | 420 | 435 | 450
Max Power [W] | 39 | 41 | 42

Table 7: Power values for gear ratio range

Stall Torque [Nm] | No Load Speed [rpm] | Max Power [W] | Energy Used [J] | Deployment Time [s] | Retraction Time [s]
0.69 | 3650 | 39.4 | 558.1 | 18.2 | 19.4
Max Damping Torque [Nm] | Max Speed [rad/s]
0.82 | 72.9

The selected number of stages was determined to be 3, with the initial stage consisting of the worm and wheel followed by 2 spur gear stages. When justifying the number of stages, an optimisation between reducing efficiency losses and minimising the size of the gearbox was considered. A rough calculation was made for a 3-stage gearbox to achieve a velocity ratio of 420. As an initial iteration, the velocity ratio per stage was selected as followed: 30:1 (worm), 4:1, 3.5:1.

According to KHK gears, the minimum number of teeth free of undercutting in a stock spur pinion for a standard pressure angle of 20° is 17 [14]. The repercussions of undercutting lead to a reduction in strength and also shortens the line of contact between meshing gears [15]. With a module of 1, the initial 3-stage configuration resulted in a total number of 192 teeth, including the pinion with a maximum gear diameter of 68mm. Consequently, when applying the same calculations to a single-stage system, the number of teeth calculated on the wheel was 7140 with a 7.14m diameter. Note that multi-stage gearboxes are typically designed with having the highest gear ratio at the input and a lower ratio at the output [16], explaining the decrease in gear ratios per stage.

The problem with this configuration is that during each revolution of the wheel, the same teeth in each of the meshing gears are always in contact with one another. Due to this, the wear is not evenly distributed amongst all the teeth and subsequently results in the shortening of the gear's life. To counteract this, the velocity ratio in each of the stages should have a hunting tooth gear combination. Thus, the improved gear ratios for each stage taking teeth hunting into account were: 30:1 (Worm), 70:17, and 58:17. Combined, this had a velocity ratio of 421.45, which is within the mentioned required range. The total number of teeth was calculated to be 192 including the 2 pinions in stages 2 and 3.

As the angular velocity of each stage decreases, the torque increases and therefore the tangential force experienced by the gears increase per stage. Varying the module in each stage was implemented to manage the increase in load. Applying (6) with the pinion angular velocity found in table 1 in stages 2 and 3, and calculating the corresponding power output, a module of 2 and 2.5 was determined respectively.

The number of starts in the worm was finalised to be 2. Applying the worm and wheel efficiency equation in (7), it was found that increasing the number of worms, also increases the efficiency.

Where η is worm and wheel efficiency, φ is the lead angle and f is the coefficient of friction.

D8.3. Gear Characteristics & Manufacturer

Kohara Gear Industry (KHK) was chosen to be the manufacturer for gears as they provided an extensive selection and the required spur, worm and wheel gears based on the determined specifications. Prioritising cost and performance, the material chosen for spur gears was S45C steel. This is the most abundant material found in gears which directly reduces costs and displays a high strength-to-weight ratio, resistance to wear and the ability to enhance the physical properties through methods of temperature treatment [17]. KHK also includes a gear calculator which substantially simplifies loading calculations. Values for tangential and separating force which were determined using the calculator can be found in Table 8 and were calculated with a safety factor of 1.2, ensuring the loads experienced in the gears can be comfortably transmitted. The selected gears can be found in the bill of materials (Table 9). KHK didn’t provide prices for the gears, therefore the cost of gears was sourced by an alternative manufacturer, HPC Gears, to provide a good estimate.

D8.4. Final Design

To minimise the size of the gearbox, overlapping lay shafts were used as seen in the Technical Drawing 4. A linear arrangement was immediately dismissed as the length of the gearbox would drastically increase. Due to the varying bore diameters between gears on the same lay-shaft, the lay-shaft was designed with a variable diameter. The lay shafts were also arranged so that they could be supported at both ends of the gearbox maximising the stability of the system.

η =

tan φ
tan θ° + φ
× 100 | (6) | θ° = tan
−1 f | (7)

### D9. Design Evaluation

Evaluation of this project considers the overall design achieved, as well as critical review of the requirements initially set out. These
outputs are analysed in
Table 10, showing that the large majority of all targets were either exceeded or in the worst case, below the
limit. | The | concept
generation stage followed a
rigorous | process | of
sketching, Lego building, Linkage modelling and MATLAB modelling. Many design concepts and iterations were tested, with the belief that the chosen design has few weaknesses. These arise from project assumptions and estimates, and areas where activities were out of the scope of the brief, not allowing development and freedom of all aspects of the system. Further work would include building a prototype to establish a definite functional design. Further extensions for mechanism design were lucrative in providing representative outputs such as material selection to gain a realistic mass and FEA stress analysis to refine the geometry and attain maximum stress capacity, key to satisfying safety priorities set at the start. With regards to technical analysis and gear ratio/motor selection, an improvement would be to optimise the selection process and aim to cover all combinations as the manual process potentially overlooked better variables for the final design.

Overall, the design was not without flaws, but successful as a proof of concept design.

Gear Stage | 1 | 2 | 3 | Gear Stage | 1 | 2 | 3
VR | 30.0 | 4.118 | 3.412 | Pinion speed, RPM | 673.0 | 22.4 | 5.45
Combined VR | 30.0 | 124 | 421.45 | Wheel speed, RPM | 22.4 | 5.45 | 1.60
Module | 1 | 2 | 2.5 | Pinion torque, Nm | 0.560 | 16.80 | 69.2
Pinion teeth / Worm Starts | 2 | 17 | 17 | Wheel torque, Nm | 16.80 | 69.2 | 236.0
Pinion PCD, mm | 16.0 | 34.0 | 42.5 | Pinion torque with losses, Nm | 0.391 | 11.73 | 63.8
Wheel teeth | 60 | 70 | 58 | Wheel torque with losses, Nm | 11.73 | 63.8 | 208.9
Wheel PCD, mm | 60.1 | 140.0 | 145.0 | Allowable tangential force, kN | 0.536 | 2.12 | 3.31
Bore diameter pinion, mm | - | 12 | 15 | Tangential force, kN | 0.3901 | 0.911 | 2.88
Bore diameter wheel, mm | 10 | 18.0 | 20.0 | Seperating force, kN | 0.1420 | 0.3316 | 1.049
Efficiency, % | 69.8 | 96.0 | 96.0 | Resultant force, kN | 0.4151 | 0.970 | 3.07
Combined efficiency, % | 69.8 | 92.2 | 88.5
Part | Part number | Source | Quantity | Cost per unit (£) | Total cost (£)
Alloy steel 4140 plate | AMS-S-6395 | Metal Supermarkets | 5 | 4.58 | 22.90
Alloy steel 4140 round bar | AMS-S-5626 | Metal Supermarkets | 5 | 1.34 | 6.70
Bushings | 748-594 | RS Components | 14 | 2.10 | 29.40
Deep groove ball bearing | 619-0171 | RS Components | 10 | 2.26 | 22.60
Motor | NSA-I 0 390 204 092 | Bosch | 1 | 42.32 | 42.32
Ultrasonic sensor | 237-0783 | RS Components | 1 | 10.85 | 10.85
Hall effect sensor | 479-6878 | RS Components | 1 | 10.43 | 10.43
Air flow sensor | 619-1938 | RS Components | 1 | 93.40 | 93.40
Capacitive sensor | 184-5598 | RS Components | 1 | 23.51 | 23.51
Worm shaft 1 | KWG1-R2 | KHK Gears | 1 | 20.42 | 20.42
Wheel 1 | CG1-60R1 | KHK Gears | 1 | 40.56 | 40.56
Pinion 1 | SSG2-17 | KHK Gears | 1 | 14.25 | 14.25
Wheel 2 | SSA2-70 | KHK Gears | 1 | 33.20 | 33.20
Pinion 2 | SSG2.5-17 | KHK Gears | 1 | 21.70 | 21.70
Wheel 3 | SS2.5-58 | KHK Gears | 1 | 69.61 | 69.61
Roof canvas material | A5B/DS | Haartz | 1 | 215.30 | 215.30
| | | | | 677.15

Table 10: Product Solution Specification (PSS)

Table 8: Gearing calculations and outputs

Table 9: Bill of Materials (BoM)

Requirement | Target values | Result | Requirement | Target values | Result
2 | 3000N | 3032N | 12, 13 | 80x80mm & 670x280mm | Targets met
3, 4, 5, 6 | 8mm, 20mph, 20mph respectively | Targets met -Mechatronics | 14 | 25kg | 23.5kg
7 | No. of members and joints: 25 | No. of members and joints: 20 | 15 | 300mm | 253.93mm from Linkage
8 | 600mm | 571mm | 16, 17 | Non-oxidising & recyclable | Targets met
9 | Weatherproof casing | Target met | 19 | 100% | Target met
10 | Cycle time evenly split between motion phases | Target met | 20 | £500.00 | £677.15
11 | 15s | Retract: 19.4s Deploy: 18.2s | 21 | Follow curves of base model 595 | Target met

### References

[1] Mini.co.uk. 2022. [online] Available at: <https://www.mini.co.uk/content/dam/MINI/marketUK/mini_co_uk/en_GB/brochures/MINI_F57_Convertible_Price_List_November_2018.pdf.asset.1539194089269.pdf> [Accessed 21 February 2022].
[2] 2022. How much weight can the convertible's roof hold?. [online] Available at: <https://www.bimmerfest.com/threads/how-much-weight-can-the-convertibles-roof-hold.506169/> [Accessed 13 March 2022].
[3] Snider, C., 2022. Engineering Practice Summative Project 2022.
[4] Car Throttle. 2022. How Convertibles Are Strengthened, And Why It’s Beginning To Change. [online] Available at: <https://www.carthrottle.com/post/how-convertibles-are-strengthened-and-why-its-beginning-to-change/> [Accessed 22 February 2022].
[5] Iopscience.iop.org. 2022. ShieldSquare Captcha. [online] Available at: <https://iopscience.iop.org/article/10.1088/1757-899X/307/1/012040/pdf> [Accessed 5 May 2022].
[6] R. Ravivarman, "Effect of Module on Wear Reduction in High Contact Ratio Spur Gears Drive Through Optimized Fillet Stress," in Recent Advances in Theoretical, Applied, Computational and Experimental Mechanics, Singapore, Springer, 2020, pp. 239-250.
[7] EduPack, G., 2021. s.l.:Ansys Inc.
[8] process, p., process, c., reaction, c., group, v., location, m. and reaction, m., 2022. US7275783B2 -Convertible roof system with dampening device - Google Patents. [online] Patents.google.com. Available at: <https://patents.google.com/patent/US7275783> [Accessed 16 April 2022].
[9] Raymond, A., 2022. Dampers: SPD n-Struts® - Motion & Speed Control Dampers | Associated
Spring Raymond. [online] Assocspring.co.uk. Available at: <https://www.assocspring.co.uk/dampers.html> [Accessed 12 April 2022].
[10] My.rs-online.com. 2022. Rotary Dampers | Adjustable Rotary Dampers | RS Components. [online]
Available at: <https://my.rs-online.com/web/c/engineering-materials-industrial-hardware/anti-vibration-levelling-components/rotary-dampers/> [Accessed 1 May 2022].
[11] Bosch-ibusiness.com. 2022. [online] Available at: <https://www.bosch-ibusiness.com/media/images/products/dc_motors/xx_pdfs_2/pac_i-buisness_e-motors_21_22_cat_en_cd2016_82263.pdf> [Accessed 12 March 2022].
[12] Kinetrol.com. 2022. [online] Available at: <https://www.kinetrol.com/pdf/cat/Rotary_Damper_2013_LR.pdf> [Accessed 1 May 2022].
[13] Kohara Gear Industry Co.,Ltd., "Involute Gear Profile," 2021. [Online]. Available: https://khkgears.net/new/gear_knowledge/gear_technical_reference/involute_gear_profile.html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,strength%20and%20c ontact%20ratio%20pose%20any%20ill%20effect.. [Accessed 2 May 2022].
[14] Tec-Science, "Undercut of Gears," 2018. [Online]. Available: https://www.tec-science.com/mechanical-power-transmission/involute-gear/undercut/. [Accessed 2 May 2022].
[15] D. Collins, "What are multi-stage gearboxes and when are they used?," 2021. [Online]. Available: https://www.motioncontroltips.com/what-are-multi-stage-gearboxes-and-when-are-they-used/. [Accessed 2 May 2022].

[16] RoyMech, "Spur Gears - Design Process," 2020. [Online]. Available: https://roymech.org/Useful_Tables/Drive/Gears.html#:~:text=The%20gear%20face%20width%20sh ould,60%25%20of%20the%20pinion%20diameter. [Accessed 2 May 2022].
[17] Gear Motions, "Selection of Gear Material," 2017. [Online]. Available: https://gearmotions.com/selection-of-gear-material/#:~:text=In%20our%20experience%2C%20at%20a,and%20the%20cost%20of%20manufac turing. [Accessed 2 May 2022].

[18]

ME Mechanical, 2017. Gruebler’s Equation. [Online]
Available at: https://mechanicalengineering.blog/grueblers-equation/#:~:text=Degrees%20of%20freedom%20for%20planar,be%20calculated%20through%20Gruebler's%20equation.&text=Most%20linkages%20used%20in%20machines,shown%20in%20figur e%20(a).
[Accessed 5 May 2022].

### Appendix

| | | | | | Graph
Stakeholder | Involvement in Evaluation | Interest in Evaluation | Influence on Evaluation | Position | Impact of Evaluation on Stakeholder | Power | Interest
Group 1 Engineering Team | High: Major involvement. Primary team for all engineering evaluation | High: Directly involved in assessing the feasability and viability of the product being designed and created. | High: Main enginering team. Success of project is directly impacted by perfomance of this team. | Main engineering team will develop all aspects of the solution from the initial requirements. Will make main decisions on most aspects of the project and provide portfolio of documentation for evaluation for Fiat and marketable specifications for customers. | Evaluation will be used as performance marker which will have effect on personal development of team members, with a positive evaluation offering potential future opportunities. | 8 | 9
FCA (Fiat Chrysler Automobiles) | High: Major resources provided to engineering subteam for R&D. | High: Potential for major return on invesment and alignment with company direction. | High: Main contributer of resources and alotted time to engineering team. Potential for project cancellation dependent on team performance and level of design. | Primary promotors and management of the project and will be providing both support and evaluation throughout all stages of project lifecycle. Will make final decision on project. | Results of final documentation and evluation of all stakeholders stance on the project will decide whether mass production and market placement commences. May offer future use of design adaptation in subsequent iterations of vehicles. | 10 | 8
Manufacturers (Production Line) | Med: Will have to be involved in determining mass manufacturing methodology for production line implementation. | Med: Potential input and advice to tailor manufacturing methods towards current available facilities. | Low: It is assumed that manufacturing line should not be a bottleneck and given a successful evaluation, any proposed manufacturing methods should be integrated into production line. | Will provide specification limits for implementing solution design, could potentially limit concepts. Beyond this, should implement required machinery dependent on project success. | Will have an effect on whether production line is overhauled at all, on a small scale or on a large scale -dependant on success of project evaluation. | 5 | 4
Suppliers (Components) | High: Major input from suppliers for available components and technology. | Med: Successful evaluation could influence future supply, availability and profit for suppliers - allowing for decreased purchase costs. | Med: Easy availability of certain components or wholesale deals could drive final solution design. Small lead times also drive faster development. | Will be providing physical hardware for product and full implementation. Influence comes from availability of components required and lead times which could influence design. | Successful evaluation results in increased business for supplier as the need to develop on a mass scale will be requested. | 6 | 3
Investors | Low: Minor input at design stage however feedback taken on. | High: Offering personal capital and potential for high return on invesment following a successful evaluation. | High: Potential risk of capital loss could cause detrimental effects to project, possible cancellation. | Will be eager for communication and updates, keeping the engineering team on their toes as risk of pulling invesment should be expected at any failures. | Positive evaluation could see more investors and thus higher capital, allowing for future opportunities within company and higher standard of quality due to increased budgets on projects. | 8 | 7
Customers | Low: Little to no input throughout engineering cycle -only exposed to final product at market. | High: Directly selling to customers thus final design will have to be satisfactory. Low: Will only need to communicated to once or twice before offical release, no need for consistent updates. | Med: As the primary intended customer, no sale could mean large losses. | Will be the primary customers to the final design however will not have too much influence on the project cycle, as design should meet the requirements of the majority, bar a niche subset who may not purchase final product. | In light of a negative evaluation, customers will not be aware of detailed specifics of the hypothetical design, and will have to 'deal' with current inefficient designs. Positive evaluation of course means increased satisfaction amongst those purchasing these vehicles and higher revenue for the company. | 2 | 2

Figure A: Stakeholder matrix

Table B: Weighted matrix for material selection

Criteria | Weight | Value | Score Value Score Value | Score | Value | Score | Value | Score | Value | Score | Value | Score
Density
(kg/m^3) | 3 | 4 | 12 | 3 | 9 | 3 | 9 | 3 | 9 | 6 | 18 | 5 | 15 | 7 | 21
Price (GBP/kg) | 4 | 7 | 28 | 4 | 16 | 6 | 24 | 5 | 20 | 2 | 8 | 1 | 4 | 3 | 12
Youngs
Modulus (Gpa) | 1 | 5 | 5 | 6 | 6 | 7 | 7 | 7 | 7 | 4 | 4 | 4 | 4 | 3 | 3
Yield Strength
(GPa) | 4 | 4 | 16 | 7 | 28 | 6 | 24 | 5 | 20 | 2 | 8 | 3 | 12 | 1 | 4
Tensile
Strength
(Mpa) | 2 | 4 | 8 | 7 | 14 | 5 | 10 | 6 | 12 | 2 | 4 | 3 | 6 | 1 | 2
Compressive
Strength
(Mpa) | 2 | 4 | 8 | 7 | 14 | 6 | 12 | 5 | 10 | 2 | 4 | 3 | 6 | 1 | 2
| Total | | 77 | | 87 | | 86 | | 78 | | 46 | | 47 | | 44

Non-Age Hardening
wrought Al-Alloys

Cast Iron,
Ductile

Low Alloy
Steel

Medium Carbon
Steel

High Carbon
Steel

Cast Al-Alloy

Age Hardening
wrought Al-Alloys
=Much More Important | =More Important | The =Same | =Less Important | =MuchLess Important
9 | 3 | 1 | 0.333 | 0.111
Criteria | Complexity | Max height | Mass | Torque | Safety | Cost | Stowed away size X | 1 | 2 | 3 | 4 | 5 | 6 | 7 | Total | %
Complexity | 1 | X | 0.33 | 1.00 | 3.00 | 0.11 | 9.00 | 3.00 | 16.44 | 13
Max height | 2 | 3.00 | X | 3.00 | 9.00 | 0.11 | 0.33 | 9.00 | 24.45 | 19
Mass | 3 | 1.00 0.33 | | X | 1.00 | 0.11 | 0.11 | 1.00 | 3.56 | 3
Torque | 4 | 0.33 0.11 1.00 | | | X | 0.11 | 0.11 | 1.00 | 2.67 | 2
Safety | 5 | 9.01 9.01 9.01 9.01 | | | | X | 1.00 | 9.00 | 46.04 | 36
Cost | 6 | 0.11 3.00 9.01 9.01 1.00 | | | | | X | 9.00 | 31.13 | 25
Stowed away size | 7 | 0.33 0.11 1.00 1.00 0.11 0.11 | | | | | | X | 2.67 | 2
| | 13.79 12.90 24.02 32.02 1.56 10.67 32.00 | | | | | | | 126.95 | 100
| | 10.9 | 10.2 | 18.9 | 25.2 | 1.2 | 8.4 | 25.2 | 100 | 126.95

Table A : Pairwise comparison weightings matrix

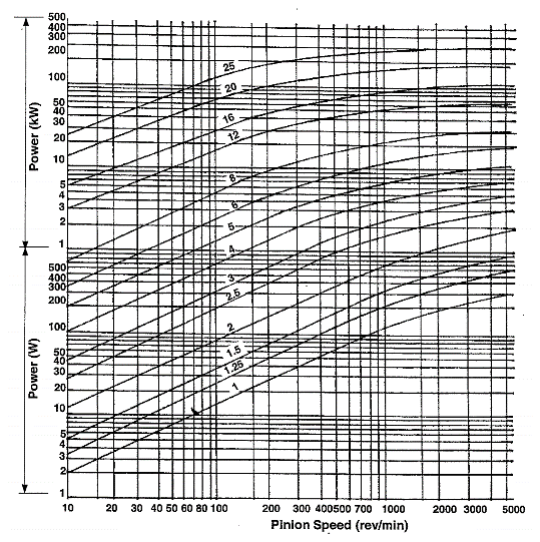
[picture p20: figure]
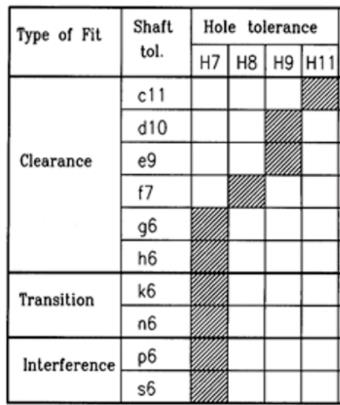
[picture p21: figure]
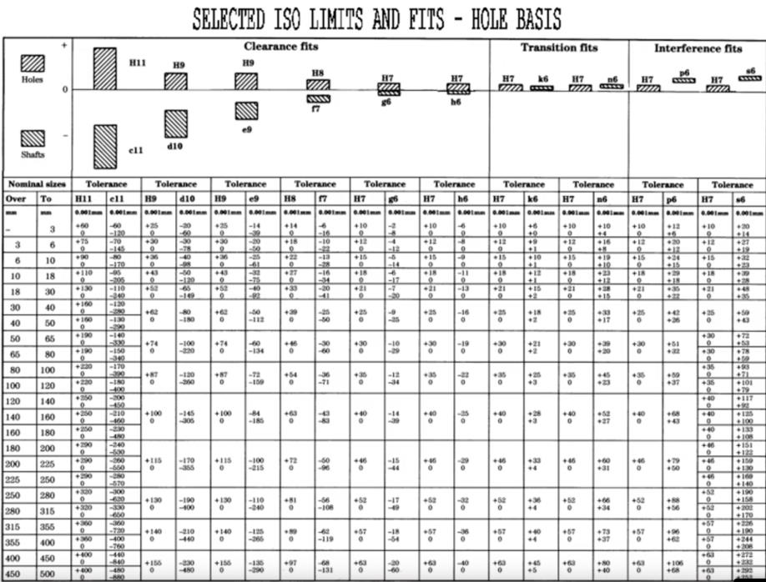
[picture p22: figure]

Table D: Table to find upper/lower bound diameter

Table C: Tolerance table

Figure B: Gear module selection charts

+

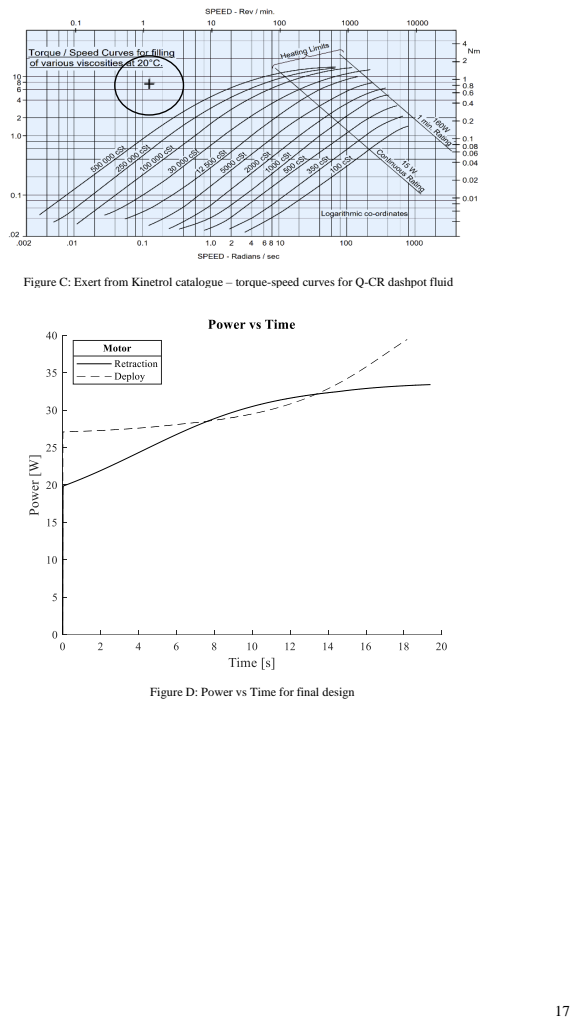
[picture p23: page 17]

Figure C: Exert from Kinetrol catalogue – torque-speed curves for Q-CR dashpot fluid

Figure D: Power vs Time for final design

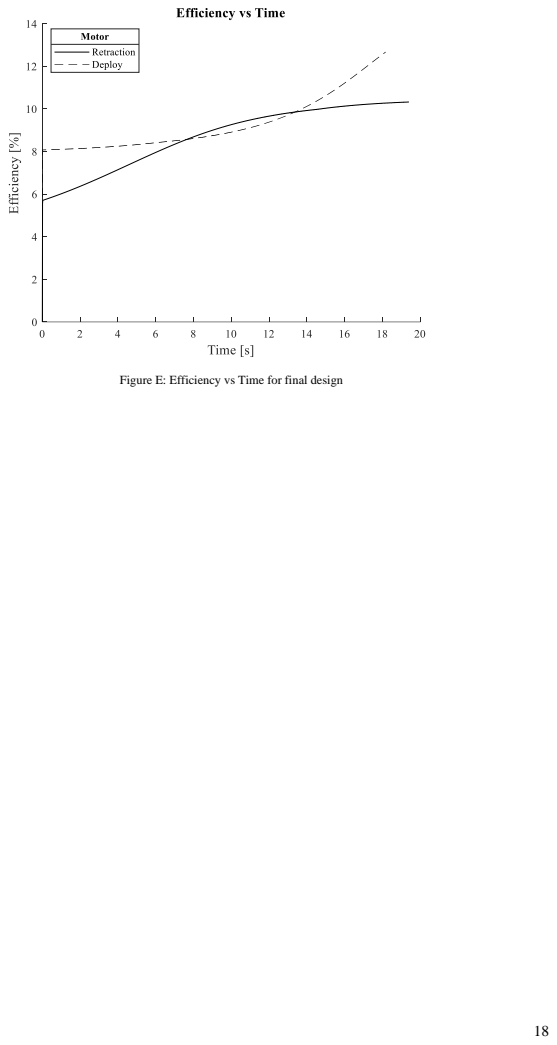
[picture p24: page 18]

Figure E: Efficiency vs Time for final design

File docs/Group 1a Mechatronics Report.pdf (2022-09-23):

1

## Safety features for an automated retractable car roof design

Group: 1a

RATIONALE FOR SAFETY FEATURES IMPLEMENTED

The following safety features and their respective sensors prioritize the safety of the passengers and prevent any permanent damage to the convertible roof mechanism.

Safety feature 1 ensures that there is sufficient space above the car to enable the convertible roof to completely open and close without interference. Insufficient space to open/close the roof could cause permanent damage to the mechanism and harm to the passengers present. It is also difficult for the driver to anticipate whether there is sufficient space above the car with the naked eye and therefore the ultrasonic sensor barrel accurately measures the available distance above the car. The longevity of the sensor itself is also considered as the top of the sensor is fitted with a grill and waterproof mesh to protect it from weathering while not sacrificing the performance of the sensor’s laser.

Safety feature 2 uses the outputs of an analogue and digital sensor to prevent strong headwind forces from damaging the convertible roof. The hall effect sensor is programmed to record wheel revolutions and hence, preventing the roof from opening at dangerous speeds. However, the hall effect sensor does not measure wind speeds which is an important consideration before initiating the opening/closing process. Consequently, an airflow sensor was chosen to measure the speed of wind flowing through the sensor for speeds up to 25mph. The convertible roof is designed to withstand wind speeds up to 20mph at a travelling speed of 20mph and hence this safety feature incorporates two different inputs from the sensors to the microcontroller to terminate the motor rotation if need be.

Safety feature 3 includes the use of a capacitive proximity sensor placed on the metal frame where the roof attaches when it is closed. This sensor ensures the travel path of the roof is clear of any possible debris that would harm the folding mechanism. This safety feature considers the safety of the passengers by preventing the possibility of any human interference such as a finger. The technology in the proximity sensor chosen allows the sensor to detect a change in capacitance in the electrical field around the metal frame when the obstacle is 8mm away from the frame. This further reduces the chances of a human body part such as a finger from getting caught in the roof’s travel path as the mechanism will terminate when the finger is just 8mm away from the metal frame. Furthermore, the presence of high winds and rain will not affect the performance of this sensor as it would not produce a high enough capacitance to produce a HIGH output to the microcontroller.

DESCRIPTION OF OPERATION

Safety feature 1: Detection of available distance above the car.
The ultrasonic sensor barrel is seamlessly placed on top of the car near the windshield with the laser pointing upwards. The sensor emits an ultrasonic beam to the surface

2

above the car and measures the time it takes for the beam to reflect off the surface and back to the sensor, hence the distance is calculated. The source code calculates the distance using the recorded duration of the laser beam’s reflection, the distance input is received by the microcontroller on port D7. When the switch to initiate the folding process is pressed, the microcontroller will signal the actuator to turn off the motor if the calculated distance is less than 253mm (swept height of the roof) meaning that there is insufficient folding space.

Safety feature 2: Monitoring of the car’s speed and headwind speed.
A magnet is fitted on one wheel with a hall effect sensor parallel to it, every time the magnet is present in the electromagnetic field of the sensor it records a revolution. The headwind speed is calculated by the airflow sensor placed within the front grill of the car. The hall effect sensor and flow controller work together to prevent the roof from opening at dangerous wind speeds sending inputs to ports D8 and A1, respectively. The Arduino code records how many times the hall effect sensor is tripped in a minute and a formula is used to determine the wind speed in mph based on the input from the airflow sensor. The microcontroller signals the actuator to turn off the motor if the calculated wheel rpm is greater than 395rpm (20mph car speed) or the calculated wind speed is greater than 20mph.

Safety feature 3: Detection of obstacles in the roof’s travel path.
The capacitive proximity sensor is placed on the metal frame of the roof attachment points. The metal frame on the top of the car acts as one plate of a capacitor which changes in value when an obstacle, such as a finger, makes contact with the metal frame. The sensor outputs LOW (0 Volts) when the capacitance is below 1μF and HIGH (5 Volts) when it is above 1μF. A human finger produces a capacitance between 1μF - 2μF and hence the sensor will not misinterpret strong winds or rain as an obstacle as it will not produce a high enough capacitance. A HIGH output from the sensor results in a HIGH input on port A2 on the microcontroller, which will signal the actuator to turn off the motor if the capacitance reading is HIGH.

SENSORS

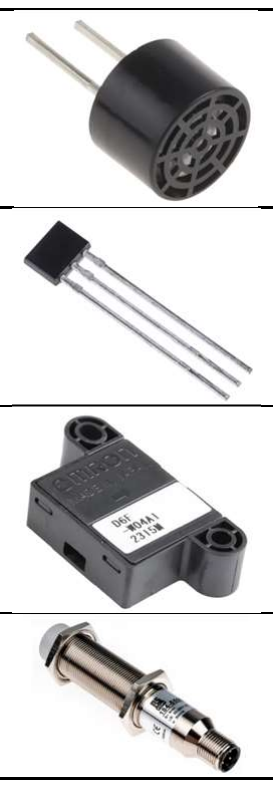
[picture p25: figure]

RS Catalogue number | Description | Image
237-0783 | Ultrasonic sensor barrel
479-6878 | Ratiometric hall effect sensor
619-1938 | Omron flow controller
184-5598 | Capacitive proximity sensor


3

HARDWARE SCHEMATIC DIAGRAM

MICROCONTROLLER EMBEDDED SOURCE CODE

/*
* Automated car roof embedded controller code
*
* refer to hardware schematic for port assignment * Author: DI
* Version 2
* Date: 19/04/2022
* Modified by DI
*/

void setup() {
// Configuration of ports as either inputs or outputs pinMode (1, OUTPUT);
pinMode (3, OUTPUT);
pinMode (2, INPUT) ;
pinMode (4, INPUT) ;
pinMode (5, INPUT) ;
pinMode (6, INPUT) ;
pinMode (7, INPUT) ;
pinMode (8, INPUT) ;
pinMode (9, INPUT) ;
pinMode (10, INPUT);
Serial.begin(9600) ;
}

int ultrasonic = 7; // Initialize pin D7 as input from ultrasonic sensor

4

int duration = 0; // Sets initial signal duration from ultrasonic sensor to 0s
int distance = (duration/2)/28.5; // Distance formula that uses MEASURED signal duration from ultrasonic sensor
int capacitive = 10; // Initialize pin A2 as input from capacitive sensor
int capacitance = 0; // Variable that reads the value from the capacitive sensor
int airflow = 9; // Initialize pin A1 as input from the air flow sensor
int halleffect = 8; // Initialize pin D8 as input from hall effect sensor
float revolutions=0; // Sets initial wheel revolutions to 0
int rpm=0; // Sets initial wheel rpm to 0
long startTime=0; // Sets start time for hall effect sensor tachometer to 0s
long elapsedTime; // Variable for total elapsed time of hall effect sensor tachometer

void loop() {
duration = pulseInLong(ultrasonic, HIGH); // Measures time it takes for one pulse from the ultrasonic sensor
capacitance = analogRead(capacitive); // Reads capacitance value from capacitive sensor
if (digitalRead(2) == HIGH) {
digitalWrite(1, HIGH) ;
analogWrite(3, 225); } // Turns on motor if switch is pressed to open the roof
else if (digitalRead(4) == HIGH) {
digitalWrite(1, LOW) ;
analogWrite(3, 255) ; } // Turns on motor if switch is pressed to close the roof
int windADunits = analogRead(airflow); // Reads airflow value from air flow sensor
float windMPH = pow((((float)windADunits - 264.0) / 85.6814), 3.36814); // Wind formula that reads input from air flow sensor and outputs wind speed in mph
startTime = millis();
rpm = (max(1, revolutions) * 60000) / millis()-startTime; // Formula that calculates rpm using hall effect sensor readings and elapsed time of wheel revolutions
if (windMPH >= 20 || rpm >= 395 || distance <= 25.3 || capacitance >= 1 || digitalRead(5) == HIGH || digitalRead(6) == HIGH) {
analogWrite(3, 0) ; } // Turns off motor if wind speed >= 20mph OR wheel rotations >= 395 RPM (car speed: 20mph) OR distance above car is <= than 253mm OR capacitance >= 1 microFarad OR if either end stop is reached
}

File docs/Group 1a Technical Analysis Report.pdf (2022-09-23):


## Fiat 595 Abarth Convertible Roof Technical Analysis

Group Members: Darian Irani (en20703), Viral Shah (di20467), Andhika Nasution (ei20239)

Group 1a

Report date: 06/05/2022

Abstract

The assignment was to design a convertible roof mechanism for the Fiat 595 Abarth with an aim to put it in direct competition with the BMW Mini Cooper convertible. This report aimed to test the feasibility of a proof of concept, with the goal of mass production. Through the several stages of the project, concepts were rigorously assessed prioritising cost and safety and maintaining level performance. Combining technical analysis with thorough mechanical design, it was decided that this system would be developed and taken forward to the engineering team at Abarth.


### TA1. Initial Model

Note: All figures in this report were produced using the ‘NSA-I 0 390 204 166’ motor with a gear ratio of 400. This was purely arbitrary and kept constant so outputs could be tracked and compared as input parameters changed and developed.

The fundamental model of the roof was
based on a single-degree-of-freedom
rotating inverted pendulum, shown in
Fig. 1. The mass of the mechanism was assumed to be a point at the end of a rod, which itself was modelled as light
and rigid. The reason why this
modelling assumption was fair is due to
how the system rotates about a fixed pivot - mirroring the motion of a pendulum. The other option was to consider all members and the canvas as uniformly distributed loads, which while more realistic, would not be feasible given the complexity of the dynamics of the system. The motion was expressed using Newton’s second law, as seen in (1). Other assumptions included the mass of the system and radius of the centre of mass – 20kg & 0.37m.
Ta − Tr = Iθ̈ | (1)

where the moment of inerti a [1] I = mr

2
[kgm²
]; θ̈ is the angular acceleration [rads⁻ ² | ]; Ta are the accelerating
torques and Tr are the resistive torques [Nm].

To solve the differential equation presented in (1), the model used MATLAB’s ode45 function, from an initial angle of 4.19 to 1.98 radians, with position and angular speed outputs. Measuring from the positive x-axis, the initial angle is 2.62 radians, however 1
2

π had to be added from MATLAB’s datum of the negative y-axis. The base model had only two torques acting on it: the motor as an accelerating torque (clockwise/anticlockwise for retraction/deployment) and gravity as a decelerating torque. These equations can be found in Appendix A.

Using this initial model, the results showed that the retraction time was 2.48s, as
depicted in Fig. 3 which is not feasible nor realistic. The motion was rather slow
initially, when working against gravity, then very quick for the second half with
gravity aiding the system. The takeaways from this model were that the operation time needed to be increased, along with a smoother and more consistent motion. These inaccuracies were consequences of initial assumptions to the model, which are presented in Table 1. The analysis process from the model was an iterative one, using the outputs of each model version to build and improve upon the next. The process can be outlined with a flowchart, seen below in Fig. 2.

Table 1: Table showing assumptions, inaccuracies, and mitigations


Figure 1: FBD of mechanism

Assumption | Innacuracy | Mitigation
Radius of centre of mass is fixed | Dynamics system hence centre of mass constantly changing | Variable radius for C.O.M added
Negligible force from headwind | This force would accelerate retraction and decelerate deployment | Aerodynamic force due to 20mph headwind added, with estimation of

modelled as inverted pendulum [3]; START; Calculate initial EOMs; Estimate initial system parameters; ode45 calculates position and speed for each timestep; Motion graphs, power, energy & efficiency values; Export linkage motion path data and categorise into member coordinates; com.m & aerodynamic.m extension scripts; Motor; Stall torque, no load speed & holding ratio; Three gear ratios; Cycle time – motion, power and efficiency graphs; Material selection for exact mass; Calculate damping EOMs; Damping coefficient; Feasible?; New cycle time, damping torque, power & eff.; YES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

Figure 2: Flowchart of how model was used for analysis and mechanical design iterations

### TA2. Modelling Extensions

TA2.1 Variable Radius of Centre of Mass (COM)

As a mitigation to initial assumptions, a variable radius of COM was implemented. 652 motion-path data points were extracted from Linkage, processed in a spreadsheet, and using (2) and (3) the radius for the COM was found for each timestep. At this stage, mass was unknown however density was assumed constant, and hence mass was replaced with length, due to proportionality, as depicted in (2) and (3).

XCoM =

∑ liXi

N
i=1
L
(2) YCoM =

∑ liYi

N
i=1
L

(3)

where N is the number of members; l is the length of each member [m]; L is the total length per timestep and (X, Y) are the midpoints of each member.

From the data, every value of radius had a corresponding value of theta. This was used in a simple lookup script that would compare the output angle from the ode45 function, against the values in the spreadsheet to a specific tolerance, and then choosing the subsequent radius. The new cycle time was 2.5s, as depicted in Fig.
3. Although not a significant difference, this new model is more accurate and reflective of real practises.

TA2.2 Aerodynamic Resistance; Variable aerodynamic force of 20mph oncoming wind was modelled onto the mechanism as per Requirement 6. This was to ensure that Requirement 11 could; Beyond 20mph, the mechanism was programmed to terminate (as detailed in the Mechatronics Report). Equation (4) represents the aerodynamic force, whilst (5) represents the aerodynamic torque acting at a radius (assumed to be the same as COM). Other assumptions also included: Laminar, incompressible and 1D flow since turbulent flow would not; effects of flow from contact with the; would; result; non-uniform

still be met even under these conditions.

be feasible to include within the model;

windshield are negligible as again, this

components acting on the specified area as well as turbulence from flow
travelling over the windscreen and into
the car; effects of lateral/angular flow
not considered – only incoming flow perpendicular to the car considered. Table 2 shows constants used in (4).

Faero = ρv

2 | yw⁄2 | (4) | Taero = Faeror | (5)

where ρ is the density of air [kgm⁻³

]; v is the wind velocity [ms⁻²
]; w is the width of the car = 1.204m; y is the swept height of the roof [m]; is the drag coefficient and r is the radius of centre of mass [m].

The swept heights at each timestep were calculated as the difference between the highest joint and the top of the
windshield (see D3.1 Fig. 3). The same lookup script from
TA2.1. selected this value for each angle. Finally, airflow
was modelled to contact the frontal surface of a rectangular prism for [2] .At first, this was modelled as a flat plate however this assumes negligible thickness and doesn’t consider the length of the roof.

Figure 3: Graphs showing retracting and deploying operation time for constant, variable radius, and aerodynamic resistance

Table 2: Constants used in Equation (4) with explanations and magnitudes

Variable | Value | Explanation
ρ | 1.225 | Density of air at sea level
| 2.05 | Drag coefficient for a rectangualar prism

Due to the streamlined mechanism design, the swept height remains low throughout the motion, hence not causing significant drag forces. These effects are portrayed by the dash-dotted curves in Fig.3, where deployment is slower and retraction is faster, as intended.

TA2.3 Damping

As seen in Fig. 3, the cycle time was far too quick, as well as the rate of change of angle turned out to be too fast. The curve is shallow in the first half as the mechanism is overcoming the resistance of gravity, whereas the latter half is very steep due to gravity aiding the mechanism. Aside from adding to the realism of the model, the main reasons for including damping were to: increase cycle time by slowing the system velocity; attain a smoother, more consistent motion and lastly, to provide extra safety by preventing damage from rapid acceleration at the end. Two forms of dampers were considered – linear and rotational.

Firstly, linear extension dampers were considered and configured as outlined in D5.1. modelled using (6). This was implemented by keeping the damping force non-zero for the angles at which extension occurred, and zero for the rest of the motion – the transition angle being found through the physical model. This was to counteract the gravitational acceleration in the second half of motion for both cycles. As observed in Fig. 4 there is a sudden change in speed when damping begins. Although this shock was expected and would be absorbed by the damper, over time this would lead to more frequent replacements due to the extra stress. The results showed that even the highest available damping coefficient offered only a 0.43s increase in cycle time.

TLD = c1ωr

2
(6) | TCRD = c2ω | (7)

, Nmsrad⁻¹; ]; ω is angular velocity [rads; connecting rod [m].; to further increase cycle time.; combining for a factor of r; , totalling an; effect of magnitude 10⁻⁴; . To eliminate this distance, a continuous rotational damper (CRD) was used as detailed in D5.2. and modelled using (7). Multiple, arbitrary; Shock

where c1, c2 are damping coefficients [Nsm⁻¹
] and r is the radius of the arc created by the

Next, to mitigate the shock, a dual-direction linear damper of the highest coefficient was used. This means that a damping torque was exerted on the mechanism in both extension and compression. Referring to Fig. 4, the first half of the motion also being dampened helps

The main loss of damping torque was due to both linear velocity and the connecting rod

damping coefficients were tested as shown in Fig. 4 and it can be noted that even the lowest
tested coefficient gives almost double the
operation time as the dual-direction linear
damper. This partially resulted in choosing CRDs over linear dampers, with other reasons being highlighted in D5.3.

TA2.4 Snow

As an extreme scenario, the roof may be attempted to be opened with a large weight of snow collected upon it. In this case, the total mass of the snow would be considered to incorporate with the COM of the mechanism. Although not an accurate assumption, this was more feasible than including the snow as a uniformly distributed load within the model. Through iteration, it was found that the roof would maintain cycle time within the stated boundaries of Requirement 11 in the PDS, with up to 11.26kg of snow on it. This is also shown in D6.3 Fig.
17. This was tested after the final parameters for the model had been selected.

Figure 4: Graphs showing retracting and deploying operation time for constant, variable radius, and aerodynamic resistance

### References

[1] R. Nave, “Hyperphysics Mechanics Rotation,” [Online]. Available: http://hyperphysics.phy-astr.gsu.edu/hbase/mi.html#:~:text=For%20a%20point%20mass%2C%20the,a%20collection%20of%20point%20masses..
[2] e. a. Baker, Table 2-2 Drag coefficient for various object shapes, 1983.
[3] Snider, C., 2022. Engineering Practice Summative Project 2022.

### Appendix

Equations:

Ta = Tmotor = − (

Tstall

ωno loa

) ωmotor + Tstall | [A]
Tr = Tgravity = −mgr cos(θ − π⁄2) | [B]

where Tstall is the torque at zero angular velocity [Nm]; ωno loa is the angular velocity at zero torque and ωmotor is the angular speed of the motor [rads⁻¹
]; m is the mass of the mechanism [kg]; g is acceleration due to gravity [ms⁻²
]; r is the radius of the centre of mass [m] and θ is the angle of the mechanism [rad].

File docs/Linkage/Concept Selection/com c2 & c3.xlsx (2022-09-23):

CONCEPT 3
deployed |  | retracted |  | members
joint | x,y | joint | x,y | AN
N | 116.563,13.256 | N | 116.563,13.256 | MF
A | 101.093,31.136 | A | 139.783,17.713 | AB
M | 100.992,13.256 | M | 100.992,13.256 | FG
F | 77.773,41.534 | F | 137.092,19.222 | BC
B | 69.056,30.446 | B | 107.745,17.018 | CD
C | 54.276,49.608 | C | 131.730,20.235 | GH
G | 37.864,40.102 | G | 97.183,17.785 | DJ
D | 7.409,47.685 | D | 84.912,23.116 | HI
J | -0.493,56.941 | J | 96.337,27.312
H | 22.480,57.985 | H | 119.296,26.000
I | -17.795,54.164 | I | 78.842,26.319
CONCEPT 2
deployed |  | retracted |  | members
joint | x,y | joint | x,y | DE
D | 96.893,9.396 | D | 96.893,9.396 | BC
E | 81.289,48.101 | E | 137.889,17.200 | CL
B | 76.312,15.272 | B | 76.312,15.272 | EN
C | 58.384,56.901 | C | 121.444,19.458 | NH
L | 23.936,60.000 | L | 87.561,26.404 | NL
J | 23.171,52.937 | J | 80.545,25.288 | JL
N | 29.100,53.843 | N | 85.405,18.663 | HJ
H | 23.936,56.900 | H | 80.009,21.288 | JI
I | -19.990,53.843 | I | 123.687,26.865

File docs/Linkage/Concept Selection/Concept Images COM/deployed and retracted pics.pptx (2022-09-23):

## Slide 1


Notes: Concept 1

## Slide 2


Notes: Concept 2

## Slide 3


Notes: Concept 3

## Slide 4


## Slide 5


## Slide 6


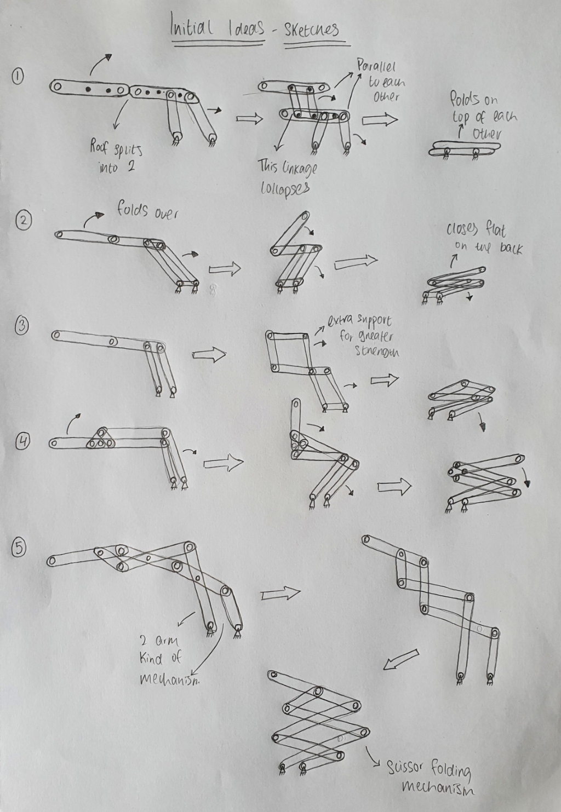
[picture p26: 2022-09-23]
docs/Initial Concept - Sketches.jpg

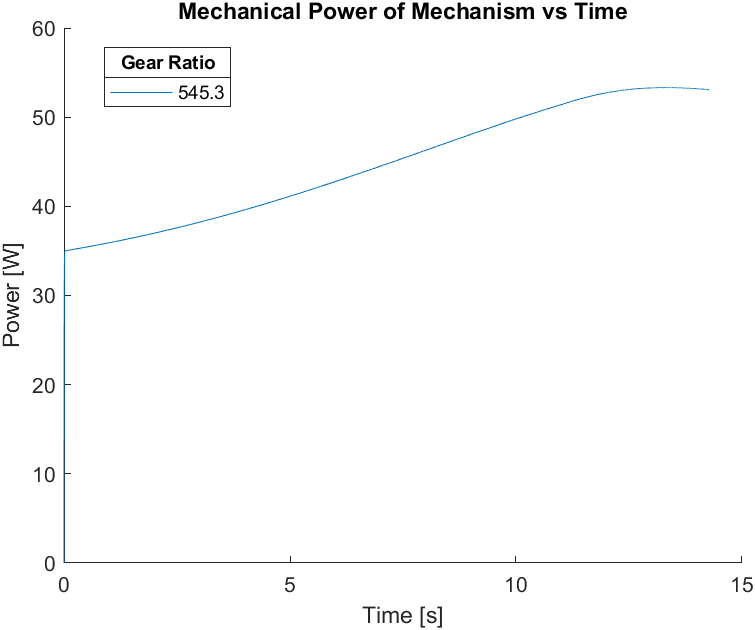
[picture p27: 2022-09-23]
docs/545 Graphs/Retract/Mechanical Power vs Time.png

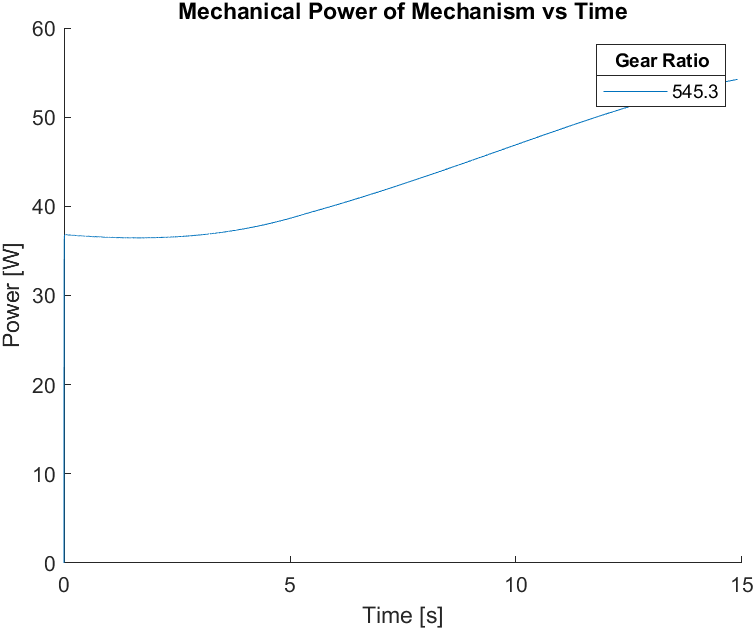
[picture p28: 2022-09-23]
docs/545 Graphs/Deploy/Mechanical Power vs Time.png

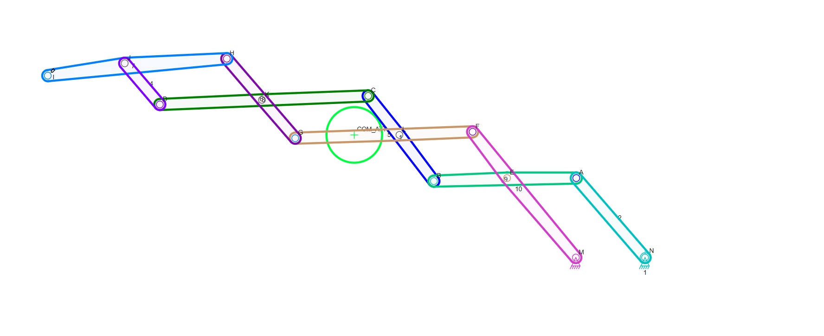
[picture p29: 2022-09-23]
docs/Linkage/Concept Selection/Concept Images COM/Concept 3 - Deployed.jpg

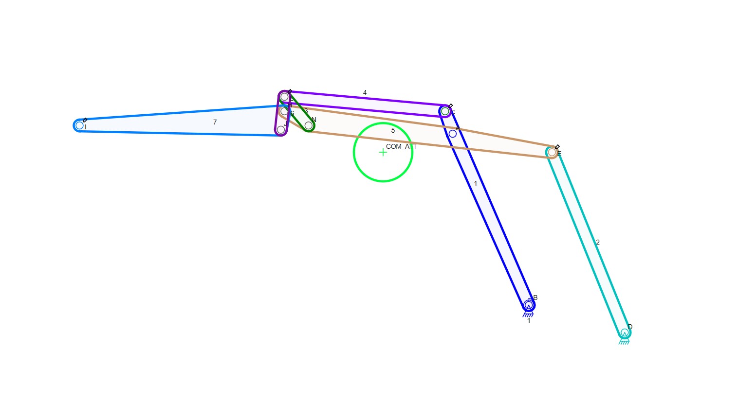
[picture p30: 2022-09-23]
docs/Linkage/Concept Selection/Concept Images COM/Concept 2 - Deployed.jpg

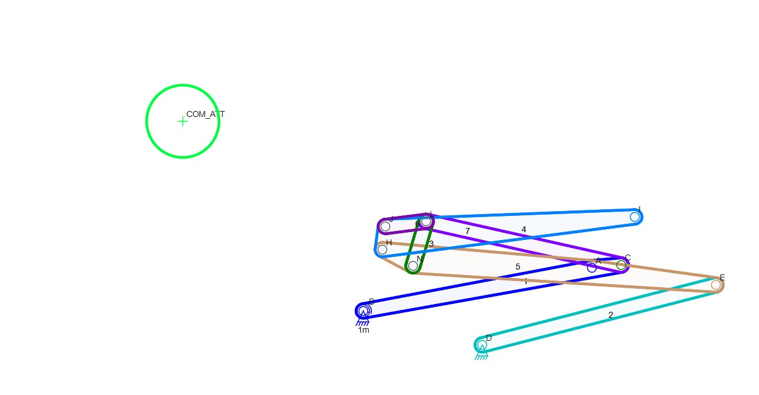
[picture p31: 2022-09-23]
docs/Linkage/Concept Selection/Concept Images COM/Concept 2 - Retracted.jpg

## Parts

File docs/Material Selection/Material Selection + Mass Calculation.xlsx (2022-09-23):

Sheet: Sheet1
Material Selection
Material | Density (kg/m^3) | Price (GBP/kg) | Youngs Modulus (Gpa) | Yield Strength (GPa) | Tensile Strength (Mpa) | Compressive Strength (Mpa) |  |  | Cast Iron, Ductile |  | Low Alloy Steel |  | Medium Carbon Steel |  | High Carbon Steel |  | Cast Al-Alloy |  | Age Hardening wrought Al-Alloys |  | Non-Age Hardening wrought Al-Alloys
Cast Iron, Ductile | 7.05E3 - 7.15E3 | 0.219 | 170 - 180 | 246 - 630 | 400 - 900 | 273 - 639 | Criteria | Weight | Value | Score | Value | Score | Value | Score | Value | Score | Value | Score | Value | Score | Value | Score
Low Alloy Steel | 7800 | 0.579 - 0.694 | 200 - 210 | 469 - 1.6E3 | 699 - 1.8E3 | 479 - 1.61E3 | Density (kg/m^3) | 3 | 4 | 12 | 3 | 9 | 3 | 9 | 3 | 9 | 6 | 18 | 5 | 15 | 7 | 21
Medium Carbon Steel | 7800 | 0.537 - 0.566 | 200 - 220 | 376 - 929 | 591 - 1.19E3 | 376 - 929 | Price (GBP/kg) | 4 | 7 | 28 | 4 | 16 | 6 | 24 | 5 | 20 | 2 | 8 | 1 | 4 | 3 | 12
High Carbon Steel | 7800 | 0.546 - 0.576 | 200 - 220 | 433 - 924 | 721 - 1.39E3 | 433 - 924 | Youngs Modulus (Gpa) | 1 | 5 | 5 | 6 | 6 | 7 | 7 | 7 | 7 | 4 | 4 | 4 | 4 | 3 | 3
Cast Al-Alloy | 2.65E3 - 2.77E3 | 1.55 - 1.68 | 69 - 76 | 118 - 263 | 193 - 341 | 109 - 251 | Yield Strength (GPa) | 4 | 4 | 16 | 7 | 28 | 6 | 24 | 5 | 20 | 2 | 8 | 3 | 12 | 1 | 4
Age Hardening wrought Al-Alloys | 2.67E3 - 2.84E3 | 2.73 - 2.89 | 68 - 76 | 241 - 520 | 288 - 571 | 245 - 521 | Tensile Strength (Mpa) | 2 | 4 | 8 | 7 | 14 | 5 | 10 | 6 | 12 | 2 | 4 | 3 | 6 | 1 | 2
Non-Age Hardening wrought Al-Alloys | 2.63E3 - 2.7E3 | 1.51 - 1.63 | 69 - 74 | 65.1 - 264 | 151 - 323 | 65.1 - 264 | Compressive Strength (Mpa) | 2 | 4 | 8 | 7 | 14 | 6 | 12 | 5 | 10 | 2 | 4 | 3 | 6 | 1 | 2
 |  |  |  |  |  |  |  | Total |  | 77 |  | 87 |  | 86 |  | 78 |  | 46 |  | 47 |  | 44
 | Selected Material: | Low Alloy Steel
Mass Calculation
Link | Volume (mm^3) From Fusion 360 | Mass (kg)
1 | 134900 | 1.05
2 | 166000 | 1.29
3 | 120600 | 0.94
4 | 188400 | 1.47
5 | 33615 | 0.26
Laterial Beams (x3) | 1133700 | 8.84
 | Total | 23.50
Joint Mass
Single Joint Mass
Number of Joints
Total
Total Considering 2 Mechanisms
Roof Mass
Material | Fabric Laminate | http://www.haartz.com/products/sonnenland-a5bds
Material Density (kg/m^3) | 1830 | PMMA | (Edupack)
 | 1160 | IIR Butyl rubber
 | 1420 | PET (30% carbon fiber)
Length (mm) | 1319.29616
Thickness (mm) | 1.7
Width (mm) | 1400 | https://www.car.info/en-se/abarth/500/595-m5-2019-18351180/specs
Volume (mm^3) | 3139924.861
Mass (kg) | 4.62
Cost per unit mass | 2.25 | PMMA
 | 1.55 | IIR Butyl rubber
 | 8.86 | PET (30% carbon fiber)
mASS | 1.92 | PMMA
 | 1.21 | IIR Butyl rubber
 | 1.49 | PET (30% carbon fiber)
Total Cost | 4.62
 | 4.309546871
 | 1.881861633
 | 13.16800755
 | 19.35941606

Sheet: Weighted Matrix
 |  | Cast Iron, Ductile |  | Low Alloy Steel |  | Medium Carbon Steel |  | High Carbon Steel |  | Cast Al-Alloy |  | Age Hardening wrought Al-Alloys |  | Non-Age Hardening wrought Al-Alloys
Criteria | Weight | Value | Score | Value | Score | Value | Score | Value | Score | Value | Score | Value | Score | Value | Score
Density (kg/m^3) | 3 | 4 | 12 | 3 | 9 | 3 | 9 | 3 | 9 | 6 | 18 | 5 | 15 | 7 | 21
Price (GBP/kg) | 4 | 7 | 28 | 4 | 16 | 6 | 24 | 5 | 20 | 2 | 8 | 1 | 4 | 3 | 12
Youngs Modulus (Gpa) | 1 | 5 | 5 | 6 | 6 | 7 | 7 | 7 | 7 | 4 | 4 | 4 | 4 | 3 | 3
Yield Strength (GPa) | 4 | 4 | 16 | 7 | 28 | 6 | 24 | 5 | 20 | 2 | 8 | 3 | 12 | 1 | 4
Tensile Strength (Mpa) | 2 | 4 | 8 | 7 | 14 | 5 | 10 | 6 | 12 | 2 | 4 | 3 | 6 | 1 | 2
Compressive Strength (Mpa) | 2 | 4 | 8 | 7 | 14 | 6 | 12 | 5 | 10 | 2 | 4 | 3 | 6 | 1 | 2
 | Total |  | 77 |  | 87 |  | 86 |  | 78 |  | 46 |  | 47 |  | 44

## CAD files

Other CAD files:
src/Assembly - Deployed v37.f3d
src/Assembly - Retracted v2.f3d
src/Component - Drawing v3.f3d
src/Gearbox Final v12.f3d

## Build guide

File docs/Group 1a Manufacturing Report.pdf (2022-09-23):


## Fiat 595 Abarth Convertible Roof Manufacturing Report

Group Members: Darian Irani (en20703), Viral Shah (di20467), Andhika Nasution (ei20239)

Group 1a

Report date: 06/05/2022

Abstract

The assignment was to design a convertible roof mechanism for the Fiat 595 Abarth with an aim to put it in direct competition with the BMW Mini Cooper convertible. This report aimed to test the feasibility of a proof of concept, with the goal of mass production. Through the several stages of the project, concepts were rigorously assessed prioritising cost and safety and maintaining level performance. Combining technical analysis with thorough mechanical design, it was decided that this system would be developed and taken forward to the engineering team at Abarth.


### M1. Component Manufacturing

The component chosen as the focus for the manufacturing section is member 5. It retains the largest dimensions and the most complex geometry making it most expensive in-house component to manufacture.

M1.1. Workpiece

Before considering manufacturing operations for the component, a low alloy steel workpiece was selected. Choosing to source stock material rather than processes such as sand casting was decided as casting would require the material to be appropriately temperature treated. Doing this in-house would rely on greater overall energy expenditure and thus, an increase in manufacturing costs. Workpiece specification depends on the maximum thickness of the component with member 4 being 12mm. One option was a flat sheet, however, by industrial standard, the maximum thicknesses produced are limited to 6.35mm [1]. Steel plates were found to be the most suitable workpiece as they come in a larger range of thicknesses between 1.6mm and 250mm [2]. Engineering Toolbox states that steel plates are typically stocked at 2000mm x 3000mm, which is sufficient for the dimensions of member 4. Sourcing alloy steel from a supplier provides options for different types of treatments such as annealed or heat-treated which both allow for easier workability and in some cases an increase in strength. A 12.5mm 4140-alloy steel plate was then sourced from Metal Supermarkets seen in the Bill of Materials in D8.4. Table 9.

M1.2. Manufacturing Process

The first manufacturing process was machining the member geometry from the stock. A CNC machining process was initially considered to allow for good control over surface finish and the ability to hold very tight tolerances. The machining rate for milling, however, was slow and restricted by the metal removal rate which can be low on alloy steels. Running a CAM simulation on Fusion 360 showed that the milling process took 3 minutes. Alternatively, a more suitable process was metal stamping which has a much higher rate of production while still retaining respectable control over tolerances. Drawbacks of metal stamping include limitations to thin materials with a maximum thickness of 12.7mm [3], however, the stock material selected has a 12.5mm thickness which is just within the acceptable limits. Since the stock material is edging towards the upper limits of the process capabilities, bigger machines and more robust tooling would be required. A temperature treated stock is also necessary to allow for maximum ductility to prevent cracking. Finally, a bespoke mould would also need to be specially designed which can connote an increase in costs, however, the substantial reduction in machining time can be justified to tolerate the high volume of production.

The next set of processes implemented a CNC machine due to its sheer flexibility and variety of cutting tools which can be used at a low cost. High-speed steel (HSS) was selected to be the tooling material for all the milling processes besides deburring as its alloyed materials allow for continuous high-speed cutting in ferrous metals. After the stamping operation, there are likely to be small imperfections which need to be deburred. Mechanical deburring was applied to one side of the part using a 60mm deburring brush. Secondly, facing off the stock with a 50mm face mill to achieve the required material thickness. Due to the stock only being 0.5mm in excess, one pass was sufficient to achieve the desired thickness as the tool was set to a maximum cutting depth of 1mm. Then, all the fillets on the component were machined using a 2-step process, as the stock required to be flipped over to mill both sides. The face mill was replaced with a 2mm radius tool, set to a 2D contour. Multiple passes were initially considered to get a roughing and then a finishing pass for a smoother surface finish. This was dismissed as the finish of the fillets was insignificant and would require a change in tooling, increasing the processing time. Reducing process time was heavily prioritised as the cost for using a CNC is rated by the hour and reducing the manufacture time allows for more components to be produced for a lower cost. After flipping the stock, a repeat of the filleting operation was completed followed by the remaining deburring process. The radius tool was then replaced by an 11.8mm drill to drill out the 3 holes. To achieve both the H7 tolerance for the hole diameter and a high-quality surface finish, a 12mm reamer was then used to repeat the drilling operation. The final operation was to machine the chamfers located on the end of the holes. A 16mm 45° countersink was fitted to the CNC and set to a 2D contour.

The processes utilising a CNC machine were simulated on Fusion 360 to determine an appropriate estimate for overall machining time. The 9 processes were found to take an estimated time of 20 minutes and 48 seconds not including the time taken to change tools and flip over the stock material. A manufacturing process flow

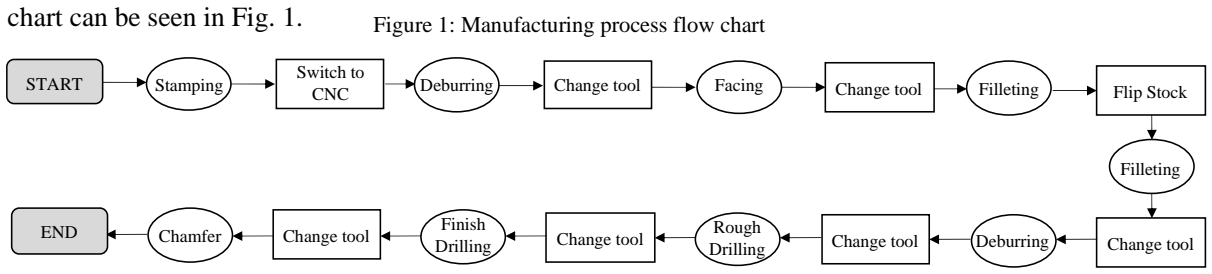
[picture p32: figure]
chart can be seen in Fig. 1.; START; Stamping; Switch to; CNC; Deburring; Change tool; Facing; Filleting; Flip Stock; Debu; Change tool Change tool; rring; Rough Drilling; Finish Drilling; END; Chamfer

### M2. Costing

The overall manufacturing cost of the part can be broadly split into 3 categories: components, assembly, and overhead as seen in Fig. 2 [4]. For this scenario, the assembly cost can be dismissed as only one component was considered in the manufacturing section. The overhead costs can be assumed to be taken forward by a different department and was also not considered.

M2.1. Component Analysis

The first cost consideration was the cost
of the stock material. CustomPartNet [5] provided a convenient stock costing estimator. The stock dimensions were inputted 650mm x 100mm x 12.5, with a run quantity of 15000 as the demand for the Abarth 595 in 2021 was 6500 [6]. A defect rate of 3% was used alongside a
cut charge of 1.5$/part and a 10%
markup to give an approximate price per

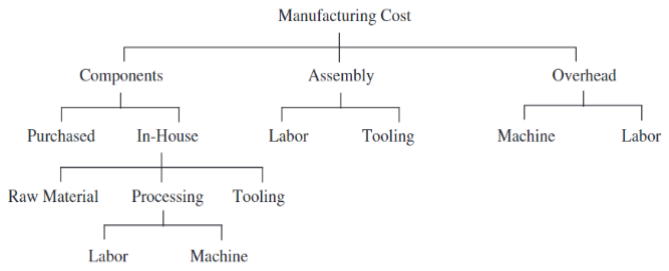
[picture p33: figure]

sheet of 5.73$ (£4.58). The cost for running a CNC machine is on average about £45/hour [7]. With the obtained value of time taken during the CNC processing of 20 minutes and 48 seconds, a value of £15.6/part was calculated. Finally, the cost of tooling was considered, and the sourced corresponding tools and their prices can be seen in Table 1. The total cost for tooling was determined to be £853.88. This value may seem high but can be justified as each tool would be utilised for large quantities of production, therefore the cost per unit part would be significantly decreased. According to Maker Industry, router bits used for metal machining should be replaced annually [8]. Therefore, an estimated tooling cost per part was calculated as £0.057.

Table 1: Tooling cost spreadsheet

It can be assumed that running a stamping machine would be more expensive than that a CNC machine. This is because the machine is expected to exert multiple tons of force requiring a lot of energy and therefore, assumed that the rate was double running a CNC machine, £90/hour. Assuming the stamping process takes 5 seconds, the running cost would total £0.125/part. The cost for the bespoke die can range between £800 to £4000 [15] and member 5 can be assumed to be within the upper end of that range due to size and thickness. Therefore, taking the value as £3000, and assuming they need to be replaced annually, the cost per part comes out to £0.2. Therefore, it can be estimated that the overall cost for manufacturing member 5 is £21.712.

Figure 1: Manufacturing process flow chart

Figure 2: Efficiency for all motors

Tool | Part number | Unit Cost [£] | Source
60mm Xebec Brush Surface [9] | A21-CB60M | 729.37 | Xebec
FEIN HSS 50mm Cutting Diameter Magnetic Drilling Hole Cutter [10] | 63134260052 | 37.83 | RS Components
2MM HSS Sc/Sh Corner Rounding Cutter [11] | ZT1155493X | 26.39 | Zoro
Bosch HSS-G Twist Drill Bit, 11.8mm x 142 mm [12] | 2608585536 | 12.12 | RS Components
Dormer HSS 12mm x Morse Taper Shank Reamer Bit [13] | B101 12MM | 32.64 | RS Components
RS PRO Countersink x16mm1 Piece [14] | 218-589 | 15.53 | RS Components
| Total | 853.88

### M.3. References

[1] A. Velling, “All About Sheet Metal – Materials, Standard Sizes & Forming Processes,” Engineering Blog, 2021.
[2] Engineering Toolbox, “Steel Plates - Size & Weight,” 2009. [Online]. Available: https://www.engineeringtoolbox.com/steelplates-weight-d_1561.html. [Accessed 1 May 2022].
[3] Aggressive Engineering Corp., “Metal Stamping Services,” 2022. [Online]. Available: https://www.aggrengr.com/metalstampingservices/#:~:text=Minimum%20material%20thickness%20for%20this,medical%2C%20construction%2C%20and%20automo tive. [Accessed 2 May 2022].
[4] Kuang-HuaChang, “Chapter 6 - Product Cost Estimating,” in Product Manufacturing and Cost Estimating Using Cad/Cae, K. Chang, Ed., Science Direct, 2013, pp. 237-294.
[5] CustomPart.net, “Machining Cost Estimator,” [Online]. Available: https://www.custompartnet.com/estimate/machining/. [Accessed 5 May 2022].
[6] How Many Left, “Abarth 595 Licenced Per Year,” 2021. [Online]. Available: https://www.howmanyleft.co.uk/?q=Abarth+595+. [Accessed 3 May 2022].
[7] Craig, “How much does CNC machining cost?,” 2020. [Online]. Available: https://www.parallelprecision.co.uk/blog/how_much_does_cnc_machining_cost. [Accessed 3 May 2022].
[8] Maker Industry, “How Long Do CNC Router Bits Last?,” 2022. [Online]. Available: https://makerindustry.com/how-long-docnc-router-bits-last/. [Accessed 4 May 2022].
[9] Xebec, “List Prices 2021,” February 2021. [Online]. Available: https://www.deburringtechnologies.com/literature/XEBEC-PL2021.pdf. [Accessed 05 May 2022].
[10] RS Components, “FEIN HSS 50mm Cutting Diameter Magnetic Drilling Hole Cutter,” Fein, [Online]. Available: https://uk.rs-online.com/web/p/magnetic-drill-bits/1797806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. [Accessed 5 May 2022].
[11] Zoro, “2MM HSS Sc/Sh Corner Rounding Cutter,” Sherwood, [Online]. Available: https://www.zoro.co.uk/shop/cuttingtools/hss-corner-rounding-cutters/2mm-hss-sc-sh-corner-roundingcutter/p/ZT1155493X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. [Accessed 5 May 2022].
[12] RS Components, “Bosch HSS-G Twist Drill Bit, 11.8mm x 142 mm,” Bosch, [Online]. Available: https://uk.rs-online.com/web/p/drill-bits/7683126. [Accessed 5 May 2022].
[13] RS Components, “Dormer HSS 12mm x Morse Taper Shank Reamer Bit,” Dormer, [Online]. Available: https://uk.rs-online.com/web/p/reamer-bits/0698152. [Accessed 5 May 2022].
[14] RS Components, “RS PRO Countersink x16mm1 Piece,” RS Pro, [Online]. Available: https://uk.rs-online.com/web/p/countersinks/0218589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. [Accessed 5 May 2022].
[15] Made-in-China, “Competitive Price Metal Stamping Mold,” [Online]. Available: https://hovol2020.en.made-inchina.com/product/YZOTgCfEaJVu/China-Competitive-Price-Metal-Stamping-Mold.html. [Accessed 5 May 2022].

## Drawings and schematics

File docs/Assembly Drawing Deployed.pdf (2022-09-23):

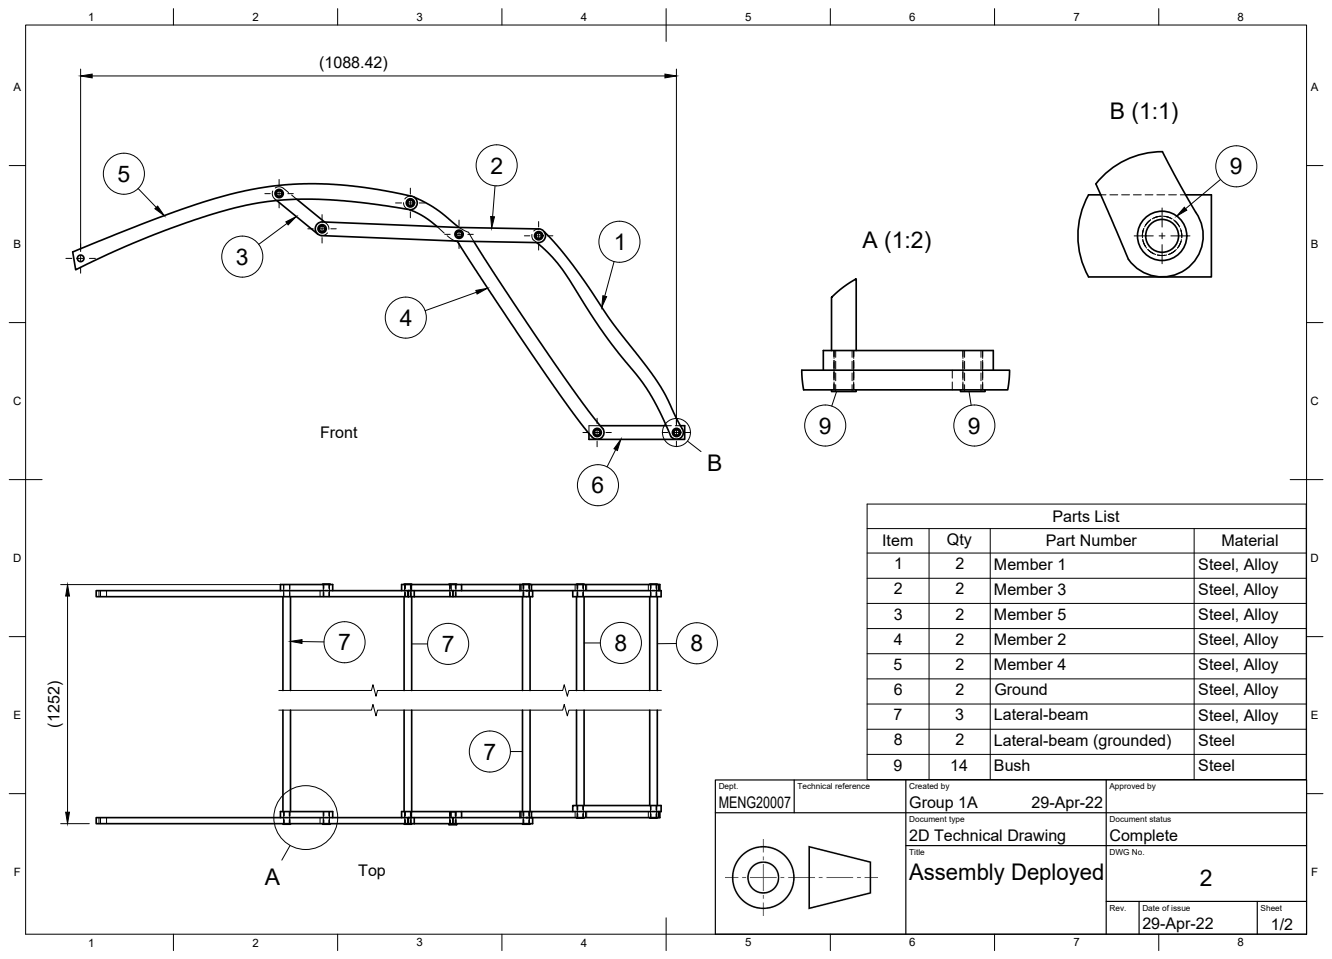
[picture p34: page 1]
Title; DWG No.; Rev.; Date of issue; Sheet; Assembly Deployed; Parts List

Item | Qty | Part Number | Material
1 | 2 | Member 1 | Steel, Alloy
2 | 2 | Member 3 | Steel, Alloy
3 | 2 | Member 5 | Steel, Alloy
4 | 2 | Member 2 | Steel, Alloy
5 | 2 | Member 4 | Steel, Alloy
6 | 2 | Ground | Steel, Alloy
7 | 3 | Lateral-beam | Steel, Alloy
8 | 2 | Lateral-beam (grounded) | Steel
9 | 14 | Bush | Steel

Dept. MENG20007 | Technical reference | Created by Group 1A 29-Apr-22 | Approved by

Document type 2D Technical Drawing | Document status Complete

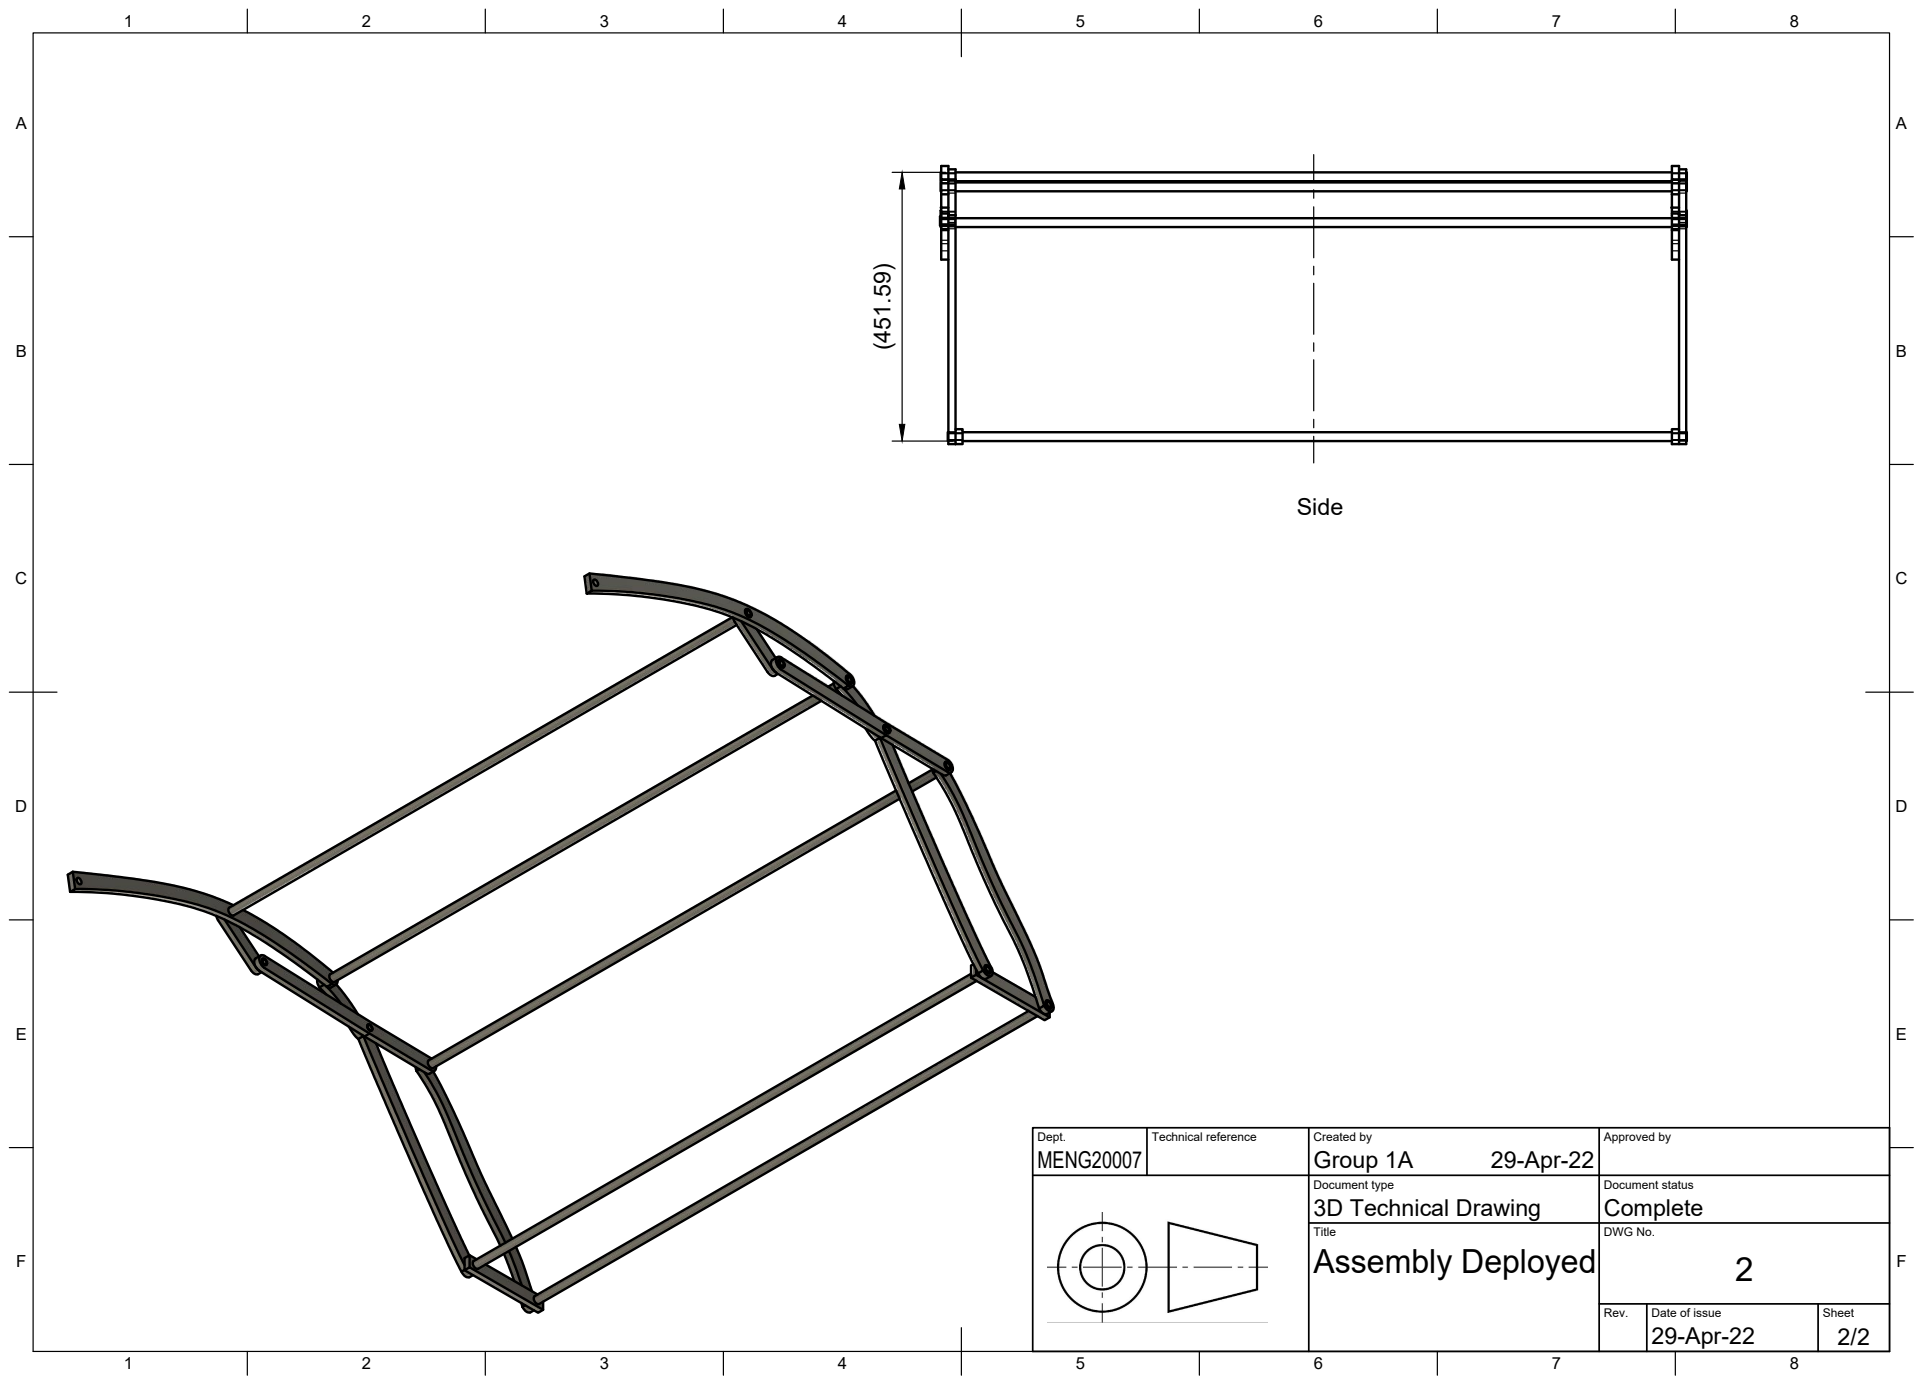
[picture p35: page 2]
Title; DWG No.; Rev.; Date of issue; Sheet; Assembly Deployed; MENG20007; Group 1A (451.59)

Dept. | Technical reference | Created by 29-Apr-22 | Approved by

Document type 3D Technical Drawing | Document status Complete

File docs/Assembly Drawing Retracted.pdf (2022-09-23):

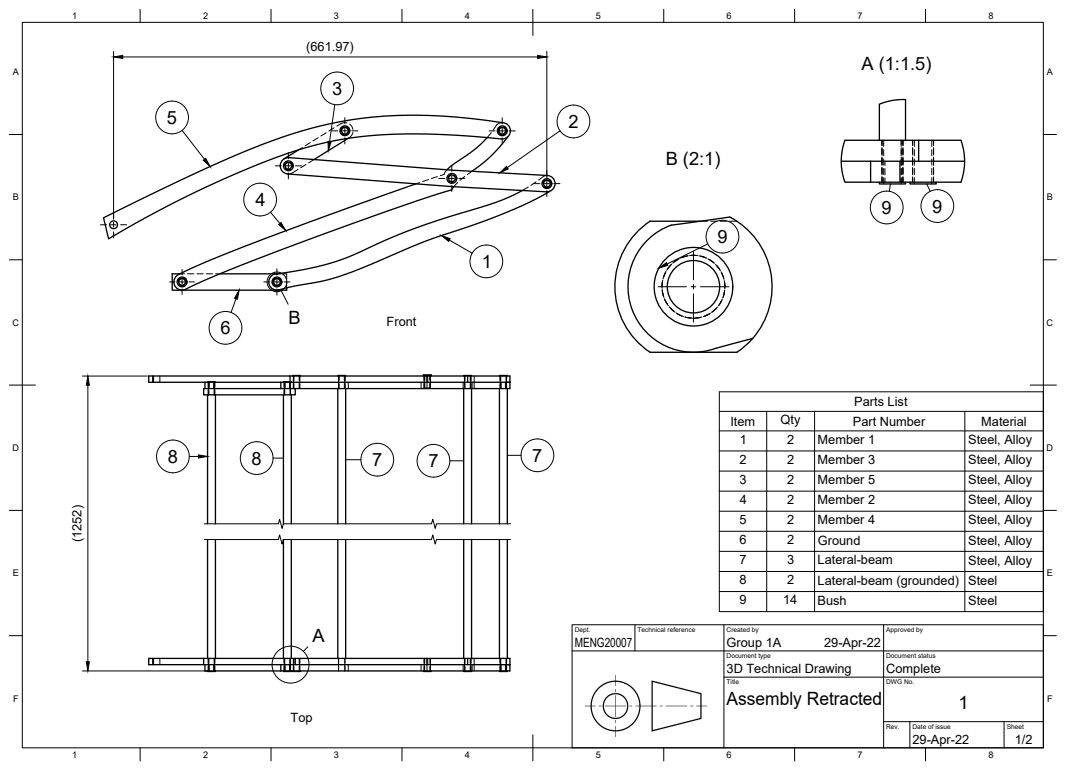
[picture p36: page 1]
Title; DWG No.; Rev.; Date of issue; Sheet; Assembly Retracted; Parts List

Item | Qty | Part Number | Material
1 | 2 | Member 1 | Steel, Alloy
2 | 2 | Member 3 | Steel, Alloy
3 | 2 | Member 5 | Steel, Alloy
4 | 2 | Member 2 | Steel, Alloy
5 | 2 | Member 4 | Steel, Alloy
6 | 2 | Ground | Steel, Alloy
7 | 3 | Lateral-beam | Steel, Alloy
8 | 2 | Lateral-beam (grounded) | Steel
9 | 14 | Bush | Steel

Dept. MENG20007 | Technical reference | Created by Group 1A 29-Apr-22 | Approved by

Document type 3D Technical Drawing | Document status Complete

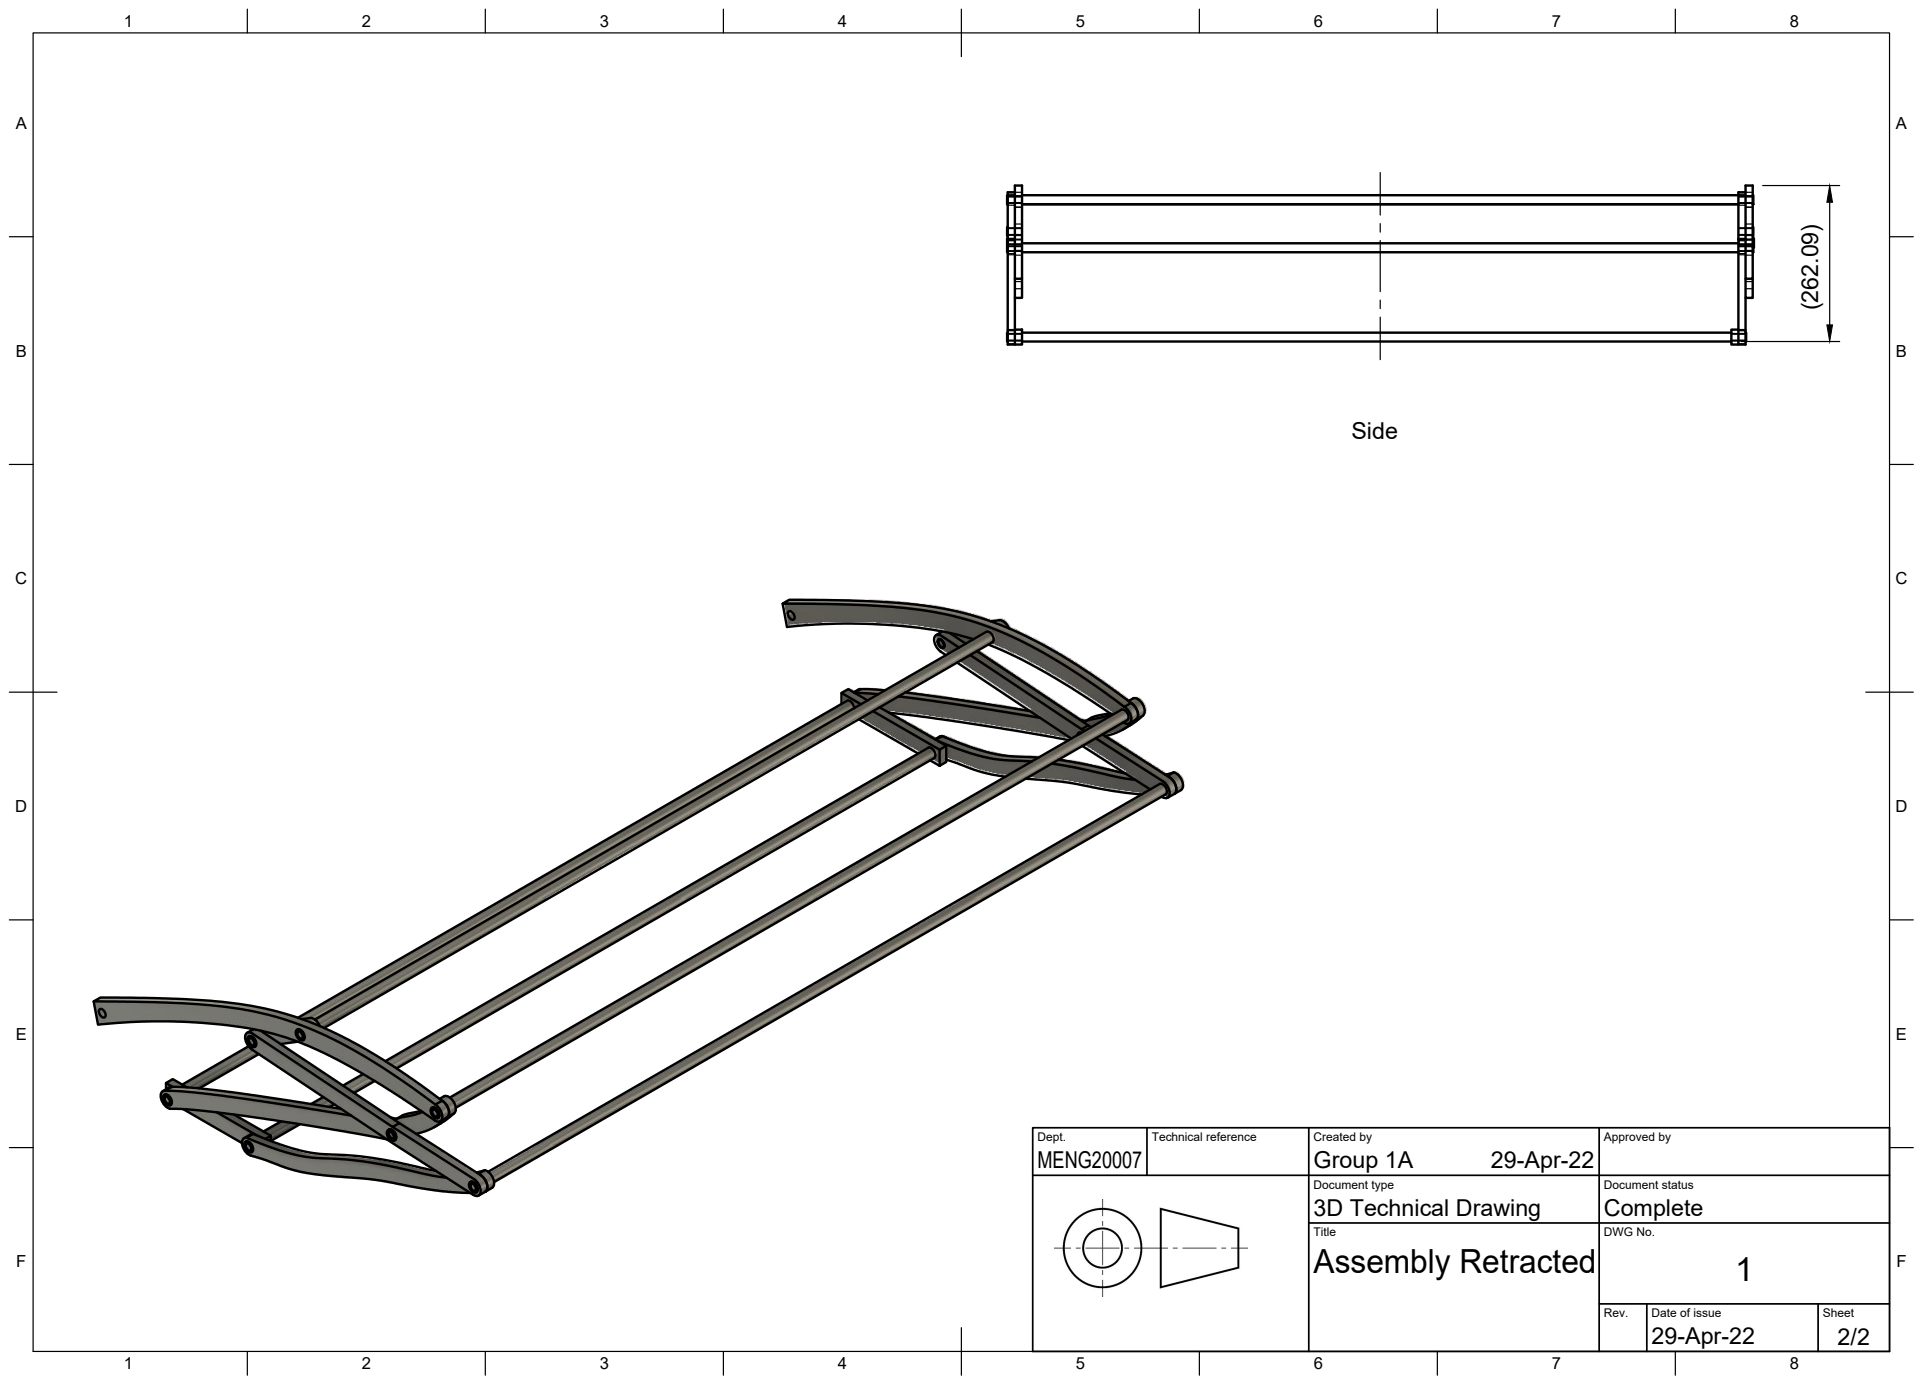
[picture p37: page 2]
Title; DWG No.; Rev.; Date of issue; Sheet; Assembly Retracted; MENG20007; Group 1A

Dept. | Technical reference | Created by 29-Apr-22 | Approved by

Document type 3D Technical Drawing | Document status Complete

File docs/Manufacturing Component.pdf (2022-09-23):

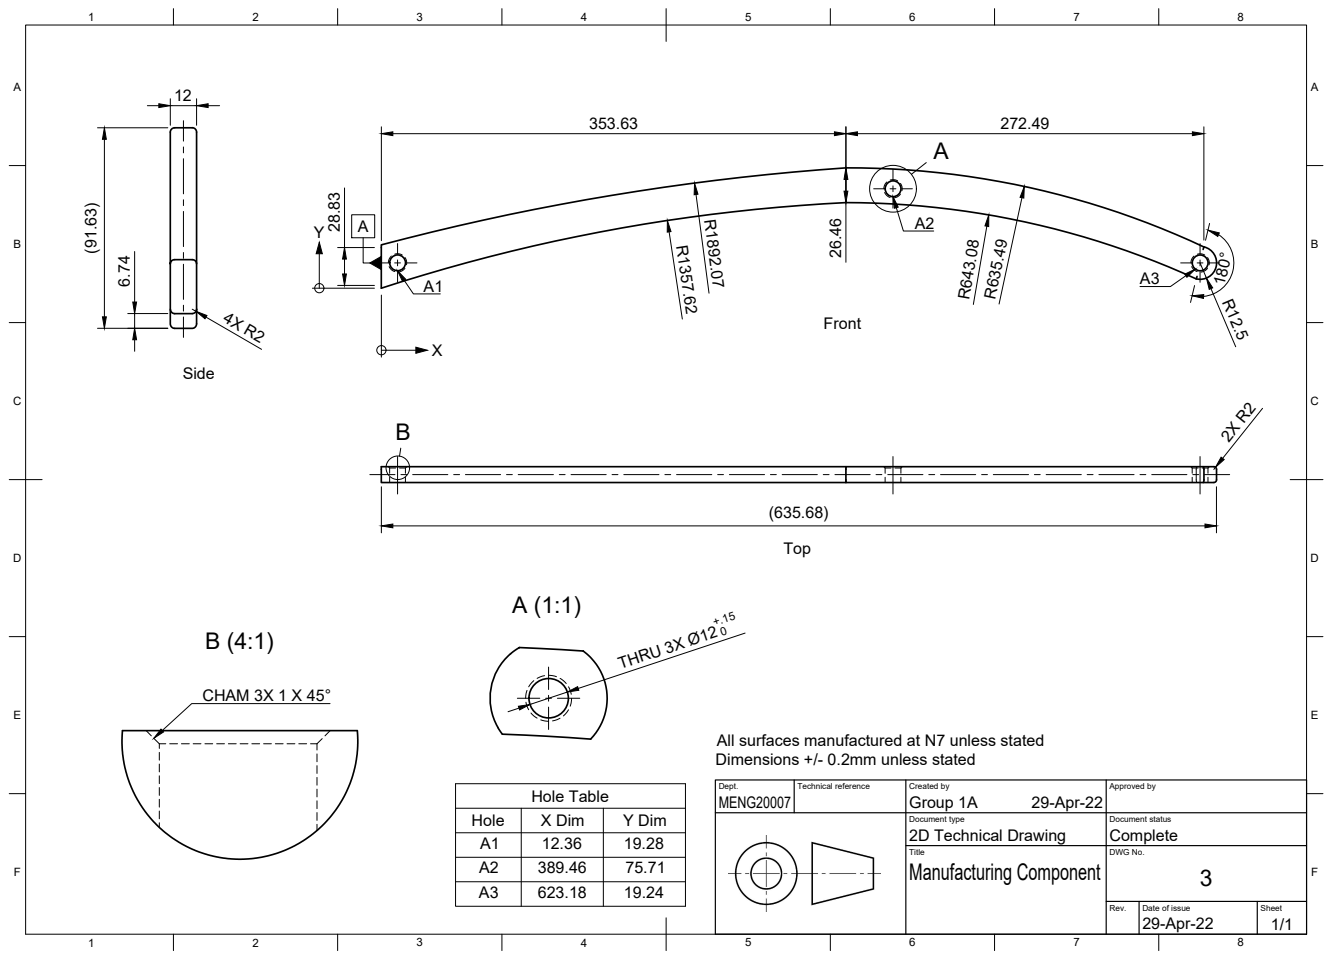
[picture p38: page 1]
Title; DWG No.; Rev.; Date of issue; Sheet; Manufacturing Component; Hole Table; THRU 3X Ø12+.15 0; CHAM 3X 1 X 45°

All surfaces manufactured at N7 unless stated
Dimensions +/- 0.2mm unless stated

Dept. MENG20007 | Technical reference | Created by Group 1A 29-Apr-22 | Approved by

Hole | X Dim | Y Dim
A1 | 12.36 | 19.28
A2 | 389.46 | 75.71
A3 | 623.18 | 19.24

Document type 2D Technical Drawing | Document status Complete

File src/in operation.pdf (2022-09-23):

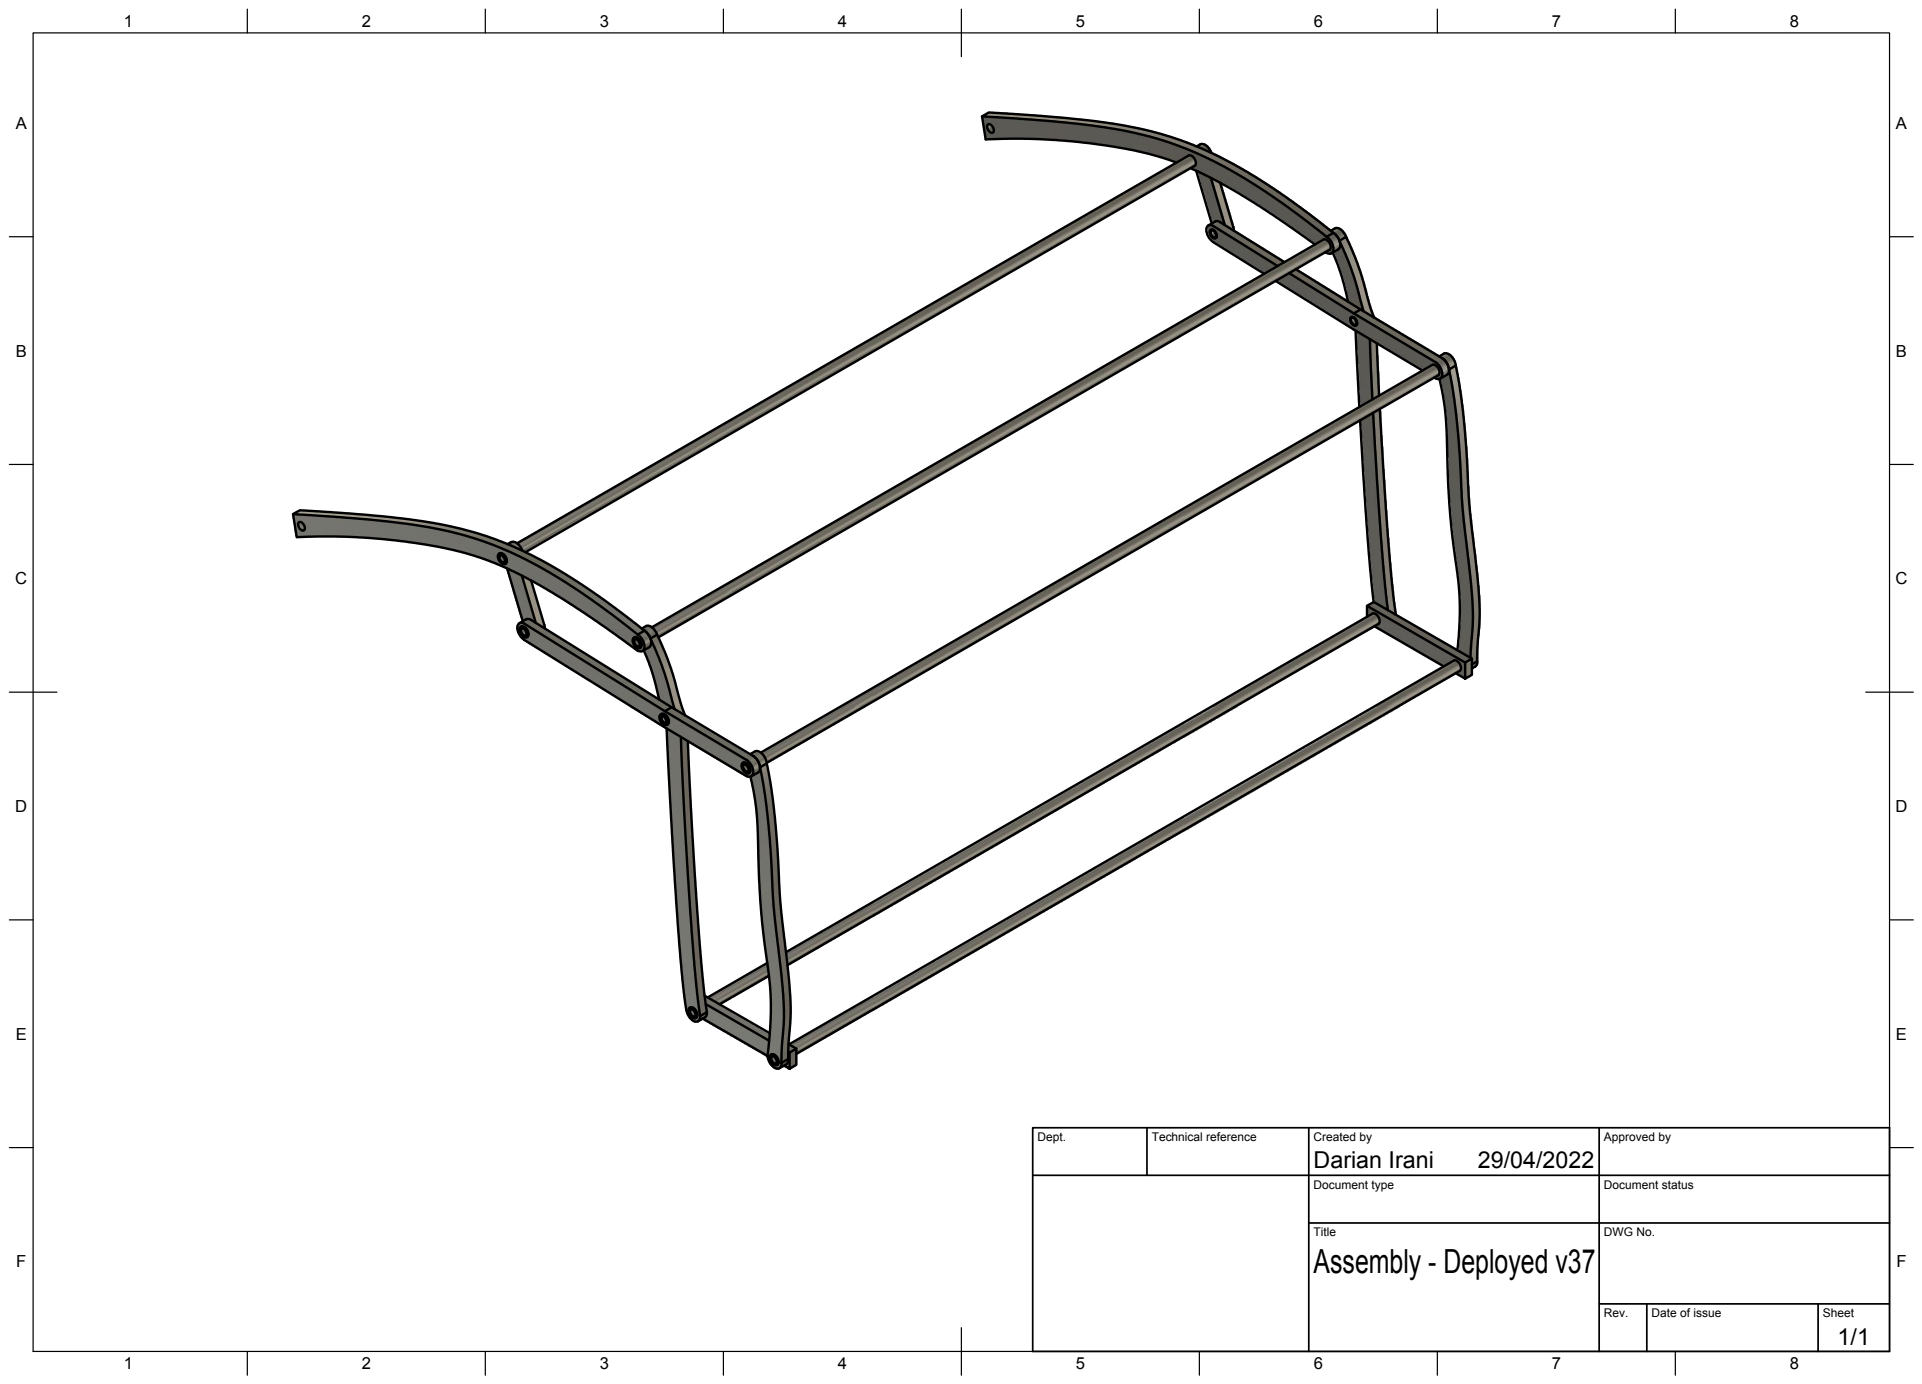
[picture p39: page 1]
Title; DWG No.; Rev.; Date of issue; Sheet; Assembly - Deployed v37

Dept. | Technical reference | Created by Darian Irani 29/04/2022 | Approved by

Document type | Document status

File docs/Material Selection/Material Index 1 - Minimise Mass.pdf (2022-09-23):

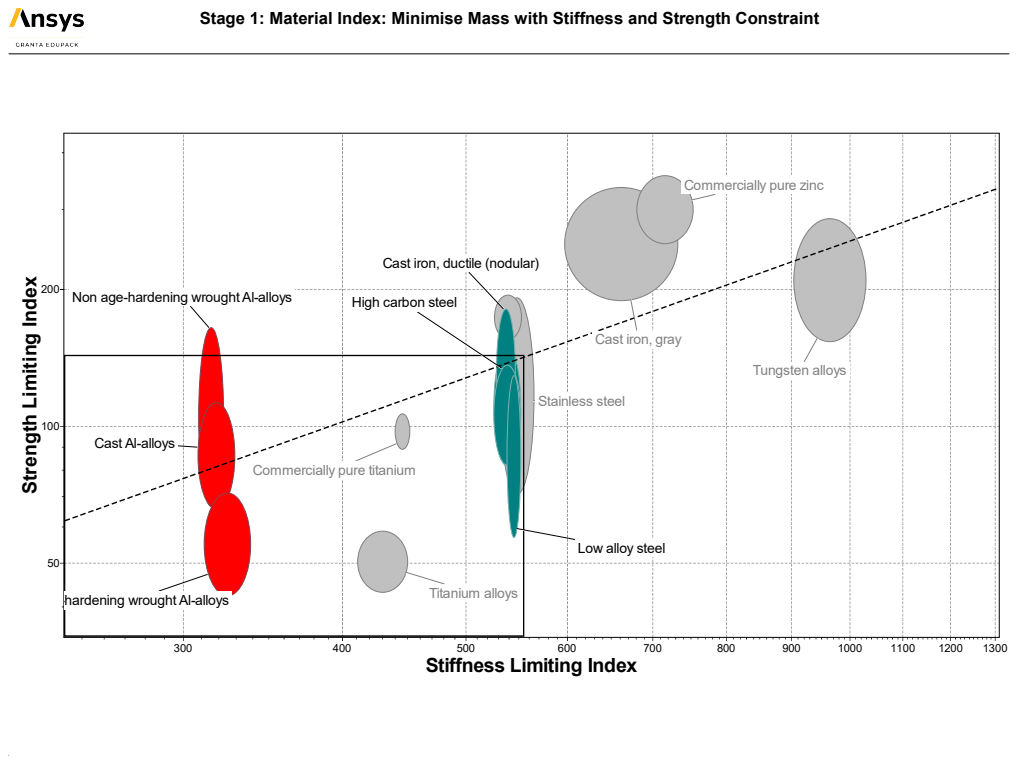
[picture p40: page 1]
1300 Strength Limiting Index; Titanium alloys; Stainless steel; Tungsten alloys

Stage 1: Material Index: Minimise Mass with Stiffness and Strength Constraint

Commercially pure zinc

Cast iron, ductile (nodular)

Non age-hardening wrought Al-alloys

High carbon steel

Cast iron, gray

Cast Al-alloys

Commercially pure titanium

Low alloy steel

Age-hardening wrought Al-alloys

Stiffness Limiting Index

Granta EduPack 2021 R2 © 2021 ANSYS, Inc. or its affiliated companies. All rights reserved.

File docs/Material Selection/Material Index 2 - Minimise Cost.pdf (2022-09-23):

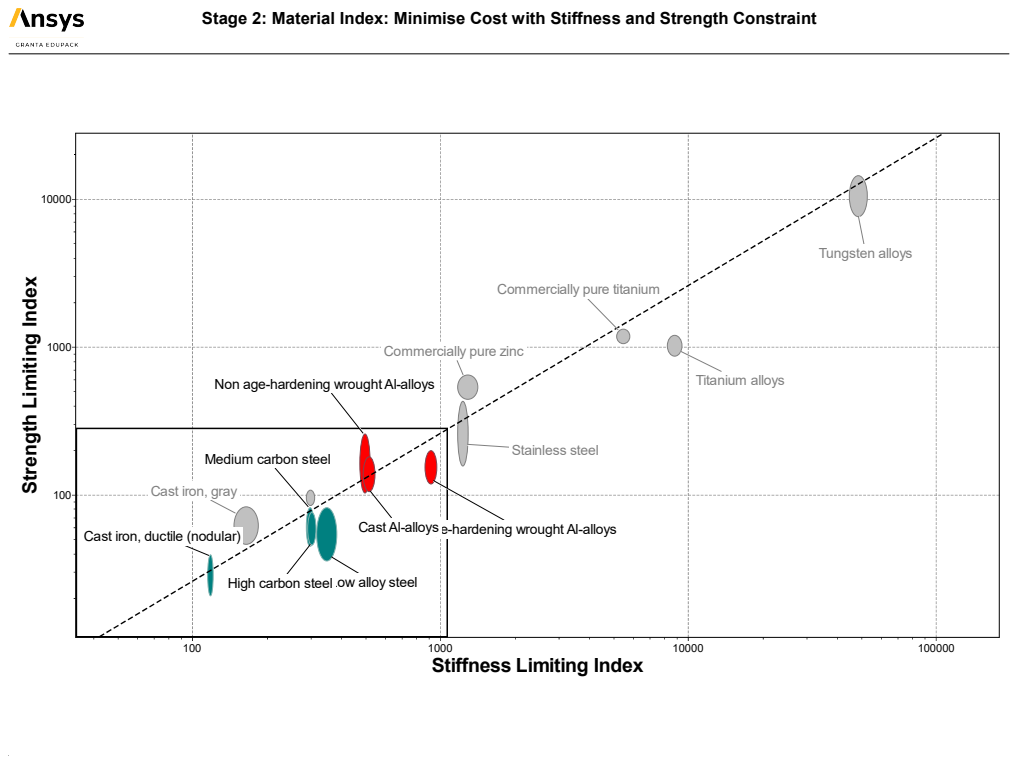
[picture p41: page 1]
100000 Strength Limiting Index; Stainless steel; Titanium alloys; Tungsten alloys

Stage 2: Material Index: Minimise Cost with Stiffness and Strength Constraint

Commercially pure titanium

Commercially pure zinc

Non age-hardening wrought Al-alloys

Medium carbon steel

Cast iron, gray

Cast Al-alloys

Cast iron, ductile (nodular)

Age-hardening wrought Al-alloys

High carbon steelLow alloy steel

Stiffness Limiting Index

Granta EduPack 2021 R2 © 2021 ANSYS, Inc. or its affiliated companies. All rights reserved.

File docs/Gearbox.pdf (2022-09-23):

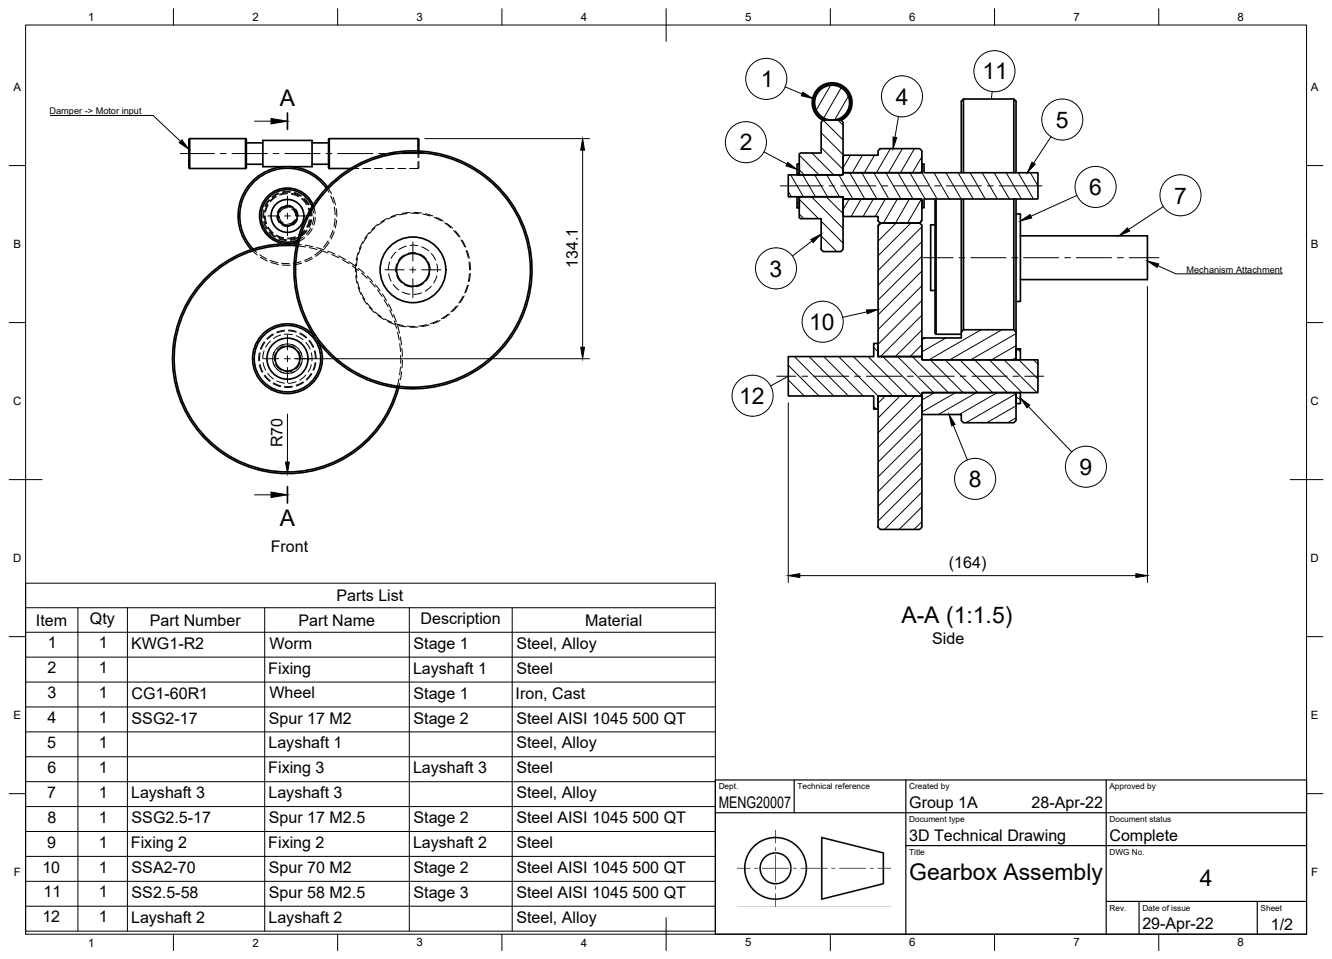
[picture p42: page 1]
Parts List; Layshaft 2; Steel, Alloy; Damper -> Motor input; Mechanism Attachment; Side R70

Item | Qty | Part Number | Part Name | Description | Material
1 | 1 | KWG1-R2 | Worm | Stage 1 | Steel, Alloy
2 | 1 | | Fixing | Layshaft 1 | Steel
3 | 1 | CG1-60R1 | Wheel | Stage 1 | Iron, Cast
4 | 1 | SSG2-17 | Spur 17 M2 | Stage 2 | Steel AISI 1045 500 QT
5 | 1 | | Layshaft 1 | | Steel, Alloy
6 | 1 | | Fixing 3 | Layshaft 3 | Steel

7 | 1 | Layshaft 3 | Layshaft 3 | | Steel, Alloy | Dept. MENG20007 | Technical reference | Created by Group 1A 28-Apr-22 | Approved by
8 | 1 | SSG2.5-17 | Spur 17 M2.5 | Stage 2 | Steel AISI 1045 500 QT
9 | 1 | Fixing 2 | Fixing 2 | Layshaft 2 | Steel
10 | 1 | SSA2-70 | Spur 70 M2 | Stage 2 | Steel AISI 1045 500 QT
11 | 1 | SS2.5-58 | Spur 58 M2.5 | Stage 3 | Steel AISI 1045 500 QT

Document type 3D Technical Drawing | Document status Complete

Title Gearbox Assembly | DWG No. 4

Rev. | Date of issue 29-Apr-22 | Sheet 1/2

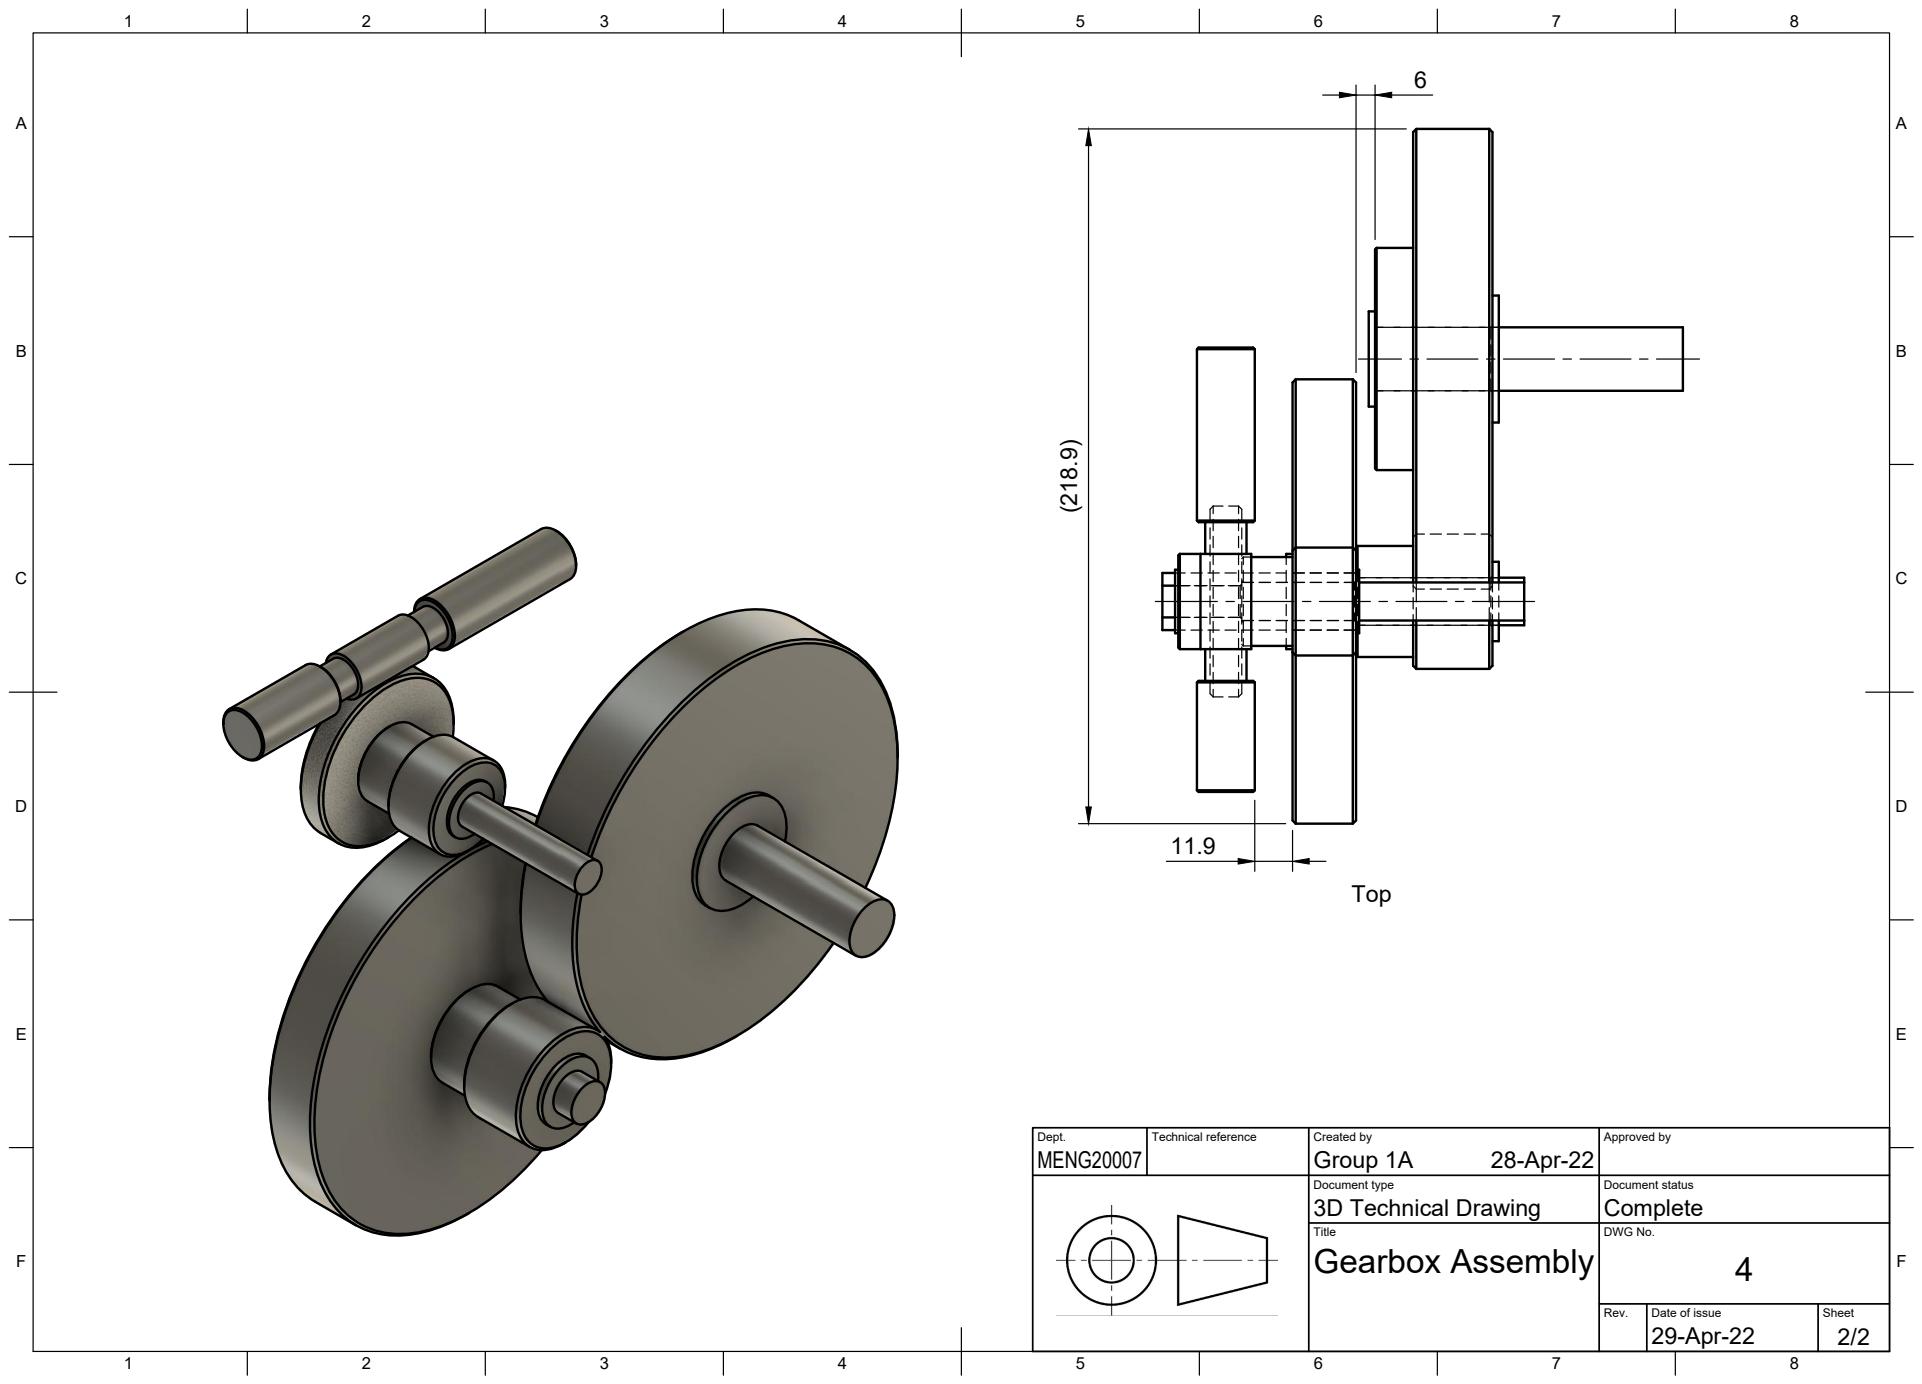
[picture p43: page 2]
Title; DWG No.; Rev.; Date of issue; Sheet; Gearbox Assembly; MENG20007; Group 1A (218.9)

Dept. | Technical reference | Created by 28-Apr-22 | Approved by

Document type 3D Technical Drawing | Document status Complete
